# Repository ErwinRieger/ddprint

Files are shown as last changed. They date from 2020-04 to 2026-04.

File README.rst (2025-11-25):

.. raw:: html

   <link rel="stylesheet" href="/images/js_css/asciinema-player.css"" type="text/css"/>

ddPrint - Adding Process control to FDM printers
=================================================

:tags: FDM, 3DDruck, 3dprinting, python, ddprint
:slug: ddprint-3d-printer-firmware

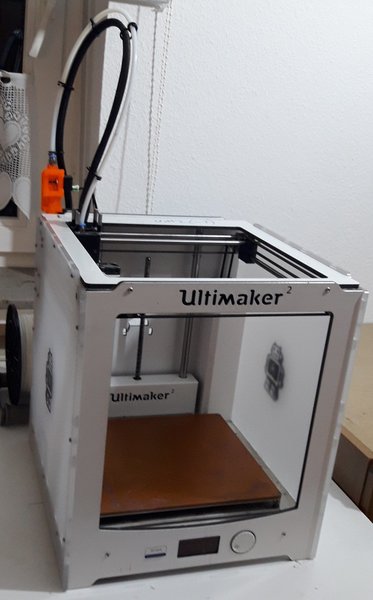
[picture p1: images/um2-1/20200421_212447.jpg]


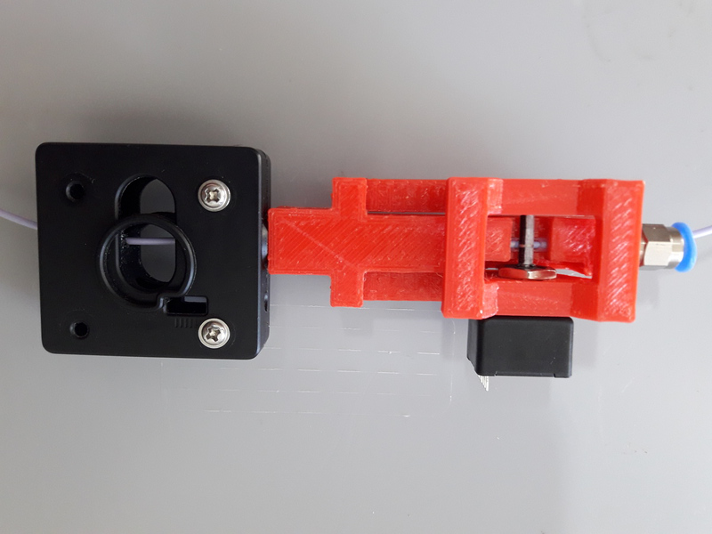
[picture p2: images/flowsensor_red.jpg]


:Note: Work in progress, documentation is incomplete and partly outdated.

Overview
++++++++++

..
   XXX LEVEL 1 XXX

DDPrint adds process control to FDM printer.

The process that is to be controlled is the process of extruding plastic.

The extrusion system includes the feeder, a bowden tube (*) and the hotend with its heater, lets call
this system the *extruder*.

Most FDM printers have no feedback on the extruder part of the printer - they are running *open loop*.

That means to find the balance of printing speed (better: volumetric flow) and hotend temperature
is difficult. Another problem of this *open loop* extrusion system is that the printer cannot react when the
hotend has difficulties to deliver the current demand of flow (for example when printing the first layer or when
the hotend is not hot enough yet).

To close the control loop we add a `sensor <#flowratesensor>`__ to measure the performance of the extruder
und use this data to control the temperature of the hotend and the speed of the printer.

The control loop is closed in two ways, an acvitve way where the speed of the printer is lowered if the hotend cannot 
deliver the demanded flowrate and the feeder begins to slip.
The other is a *feed forward* way: The flowrate sensor is used to measure the characteristics of a given filament - extruder
combination. The result of this measurement is a so called `material profile <#material-profiles>`__.

Control of hotend temperature is called `autotemp <#auto-temp>`__.

Control of printer speed is done with the `temperature-limiter <#temperature-limiter>`__ and the `flowrate-limiter <#flowrate-limiter>`__
.

(*) For the moment `bowden style printers only. <#bowden-style-printers-only>`__

.. contents::

..
   XXX LEVEL 2 XXX

Key features
+++++++++++++

* One of the main features of ddprint: using a flowratesensor 
* Automatic material profile measurement, determine *into-air* and *printing* volumetric flowrate data.
* material profiles
* auto-temp
* temperatuer-limiter.
* flowrate-limiter.
* ddprint uses Integer math instead of floating point because of the weak atmega cpu

Installation
+++++++++++++

Firmware part
-------------

Requirements, dependencies
**************************

* `Arduino-Makefile <https://github.com/sudar/Arduino-Makefile>`__
* avrdude for arduino based firmware upload 
* stm32flash for stm32 based (jennyprinter) firmware upload 

Host part
-------------

The host software is written in Python 3.

Requirements:

* python3
* python3-serial
* python3-numpy
* npyscreen (for the TUI)

Use the `scripts/ddinstall.sh` script to install the dependencies.

Usage
+++++

The host software provides a command line interface (`ddprint`) and a text based user interface (`ddprintui`).

Use the `scripts/dd-fw-upload.sh` script to upload the firmware to the printer.

There are explanatory ansciinema screencasts for the following commands:

* `ddprint getstatus` (shortform: `ddprint stat`)
* `ddprint top`
* `ddprint mon`

Architecture
++++++++++++

The software is split into two main parts:

* The host part where the cpu intensive work (gcode preprocessing, path planning, lookahead, acceleration, advance...) is done.
  The host part is written in Python 3.
* And the firmware part that runs on the ATMega Controller in the printer. This part executes the move commands from
  the host and does other things like the temperature control of the printer.

The firmware part is implemented using the `protothreads-cpp <https://github.com/benhoyt/protothreads-cpp>`__ library.

To overcome the limited memory of the atmega, the unused SD card is converted to something like a *swap device*: It buffers the received data. This decouples the USB transfer
and actual use of the received data, too.

Experimental Features
+++++++++++++++++++++

* RepRap/OctoPrint interface: There is an experimental reprap usbserial interface using a pseudo-tty to use OctoPrint as a frontend for ddPrint. Not much functionality yet: display temperatures and some SD card commands (stubs).
* `reconnect` command: To reconnect to a running printer, works after download is complete, but not if disconnected while downloading stepper data.

Flowratesensor
++++++++++++++

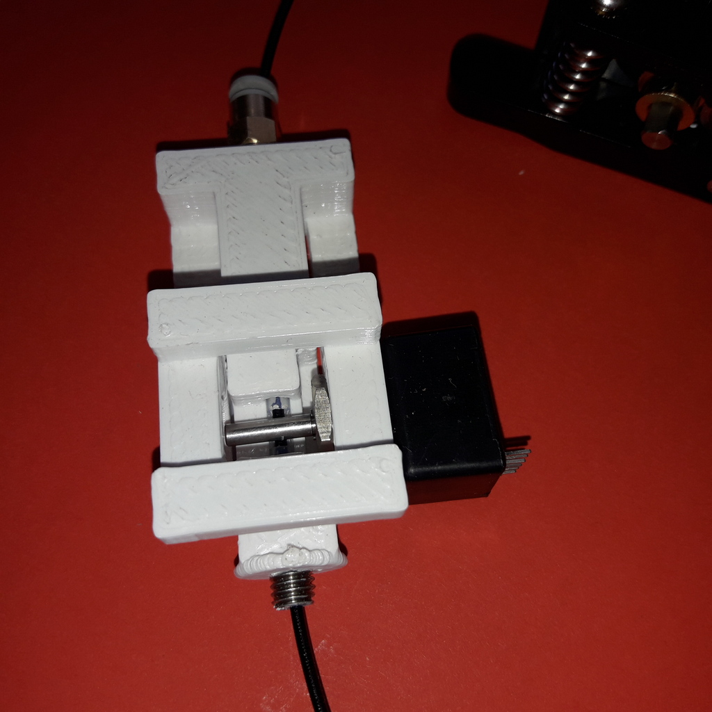
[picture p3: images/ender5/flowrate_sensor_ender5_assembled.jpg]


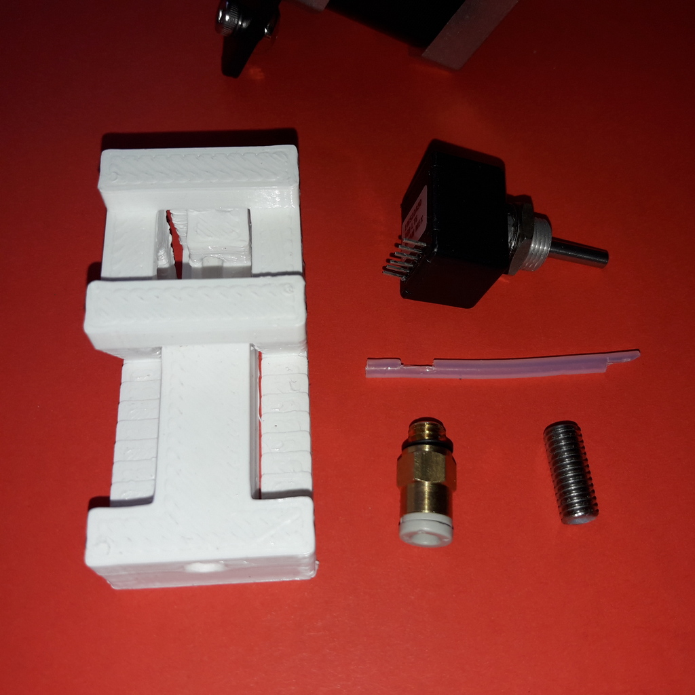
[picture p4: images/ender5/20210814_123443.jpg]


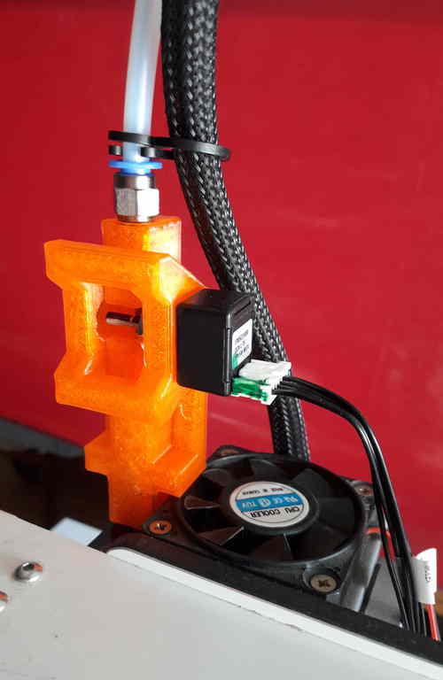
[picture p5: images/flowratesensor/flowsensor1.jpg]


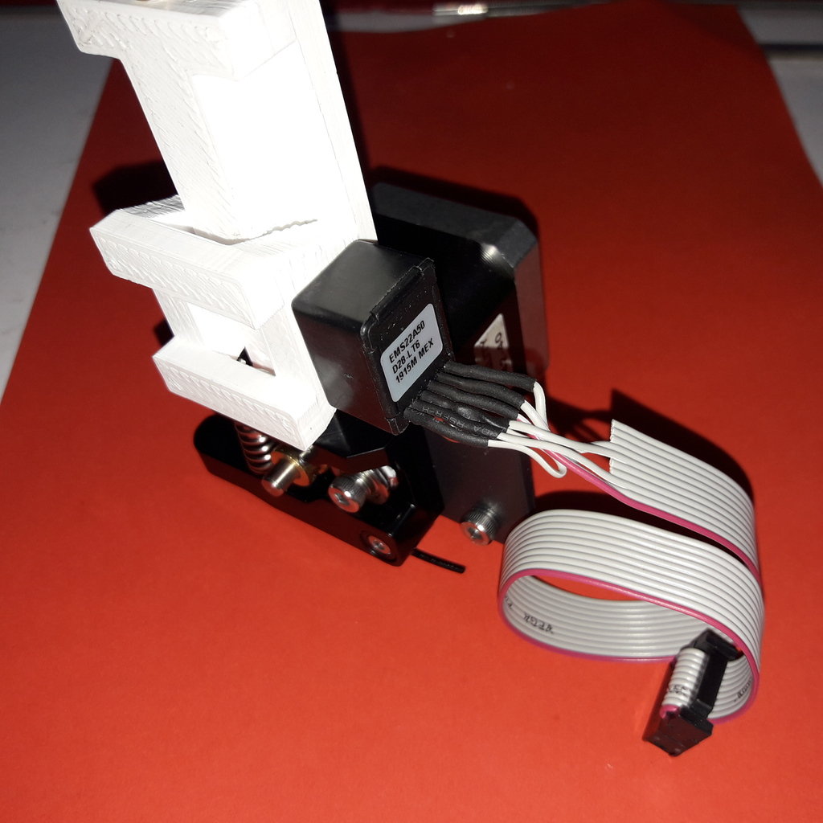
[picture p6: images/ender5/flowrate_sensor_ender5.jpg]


The flowrate sensor (FRS) is used to measure the movement of the filament. It consists of a incremental rotary encoder (Bourns EMS22) and a 3d printed housing.
The axle of the encoder is pressed onto the moving filament using a spring that is part of the FRS housing.

The distance-information from the FRS is continuously read by the firmware and is used for several tasks:

* Compute the speed of the filament and the resulting volumetric flowrate (taking filament diameter into account).
* Compare the actual volumetric flow with the nominal volumetric flow to implement the `flowrate-limiter <#flowrate-limiter>`__.
* Automatically record `material profiles <#material-profiles>`__.
* Automatically `calibrate the feeder "esteps" <#calibrateesteps>`__ (for the machine profile).
* Automatically `calibrate the FRS <#calibratefilsensor>`__ (for the machine profile, too).

More details `are here <#flowratesensor-1>`__.

Bowden style printers only?
+++++++++++++++++++++++++++

For best results, the flowrate sensor has to be placed *after* the feeder. This is easy for a bowden style printer.

For direct driver printers it should be possible but it is more difficult to add the flowrate sensor into the print head (because of
space requirements, heat, added weight and so on).

Material Profiles
+++++++++++++++++

Material (filament) profiles are used for two things in ddprint:

* They define the hotend temperature necessary to melt a given volumetric flow of filament, see `autotemp feature <#auto-temp>`__.
* The `temperature-limiter <#temperature-limiter>`__ uses the information in the material profile to slow down the print in cases
  where the hotend is not hot enough (yet) to melt the requestet amount of filament.

With other words: the material profile gives a picture of the hotend melting capacity for a given machine/filament combination - "*the printer knows its filament*".

A material profile for a given filament is created automatically by ddPrint and stored in JSON format for later use.

This filament-measurement is done in two steps:

* A best-case scenario where filament is extruded *into air*.
* And a worst-case scenario where a small testpart is printed under difficult circumstances (high backpressure because of 100% infill and small layerheight).

ddPrint comes with a python script to plot material profiles (`plot_mat_profile utility <#profile-plotting-utility>`__). Here are two examples of material profiles, one
for a PLA filament and one for a PETg filament:

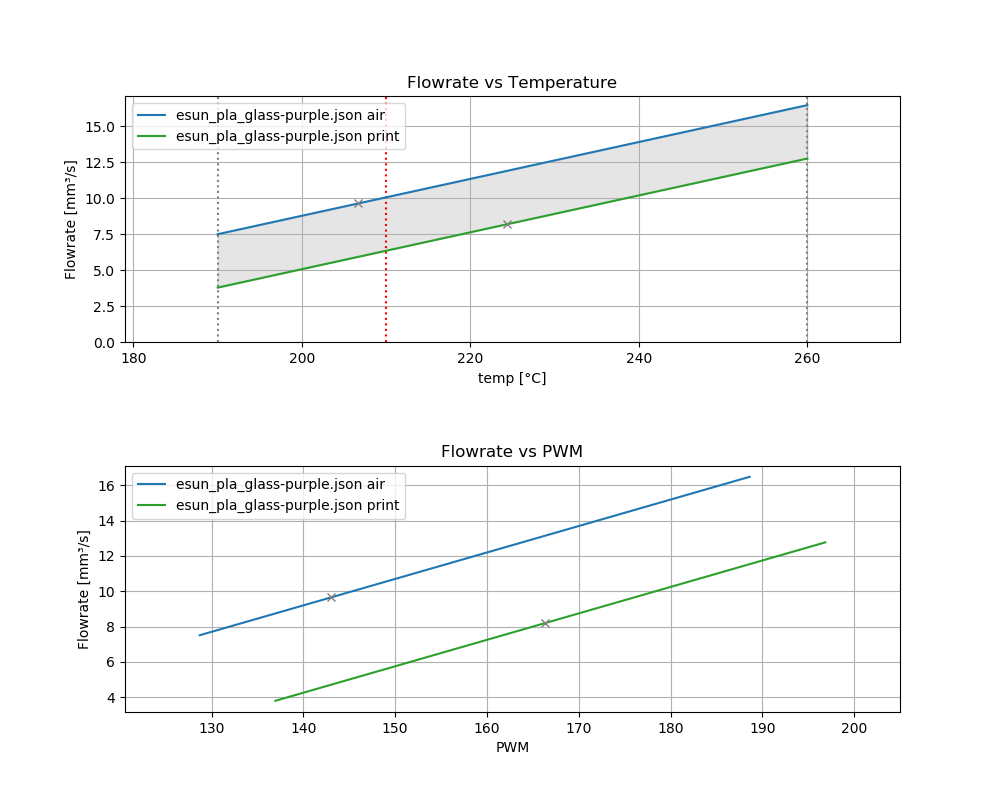
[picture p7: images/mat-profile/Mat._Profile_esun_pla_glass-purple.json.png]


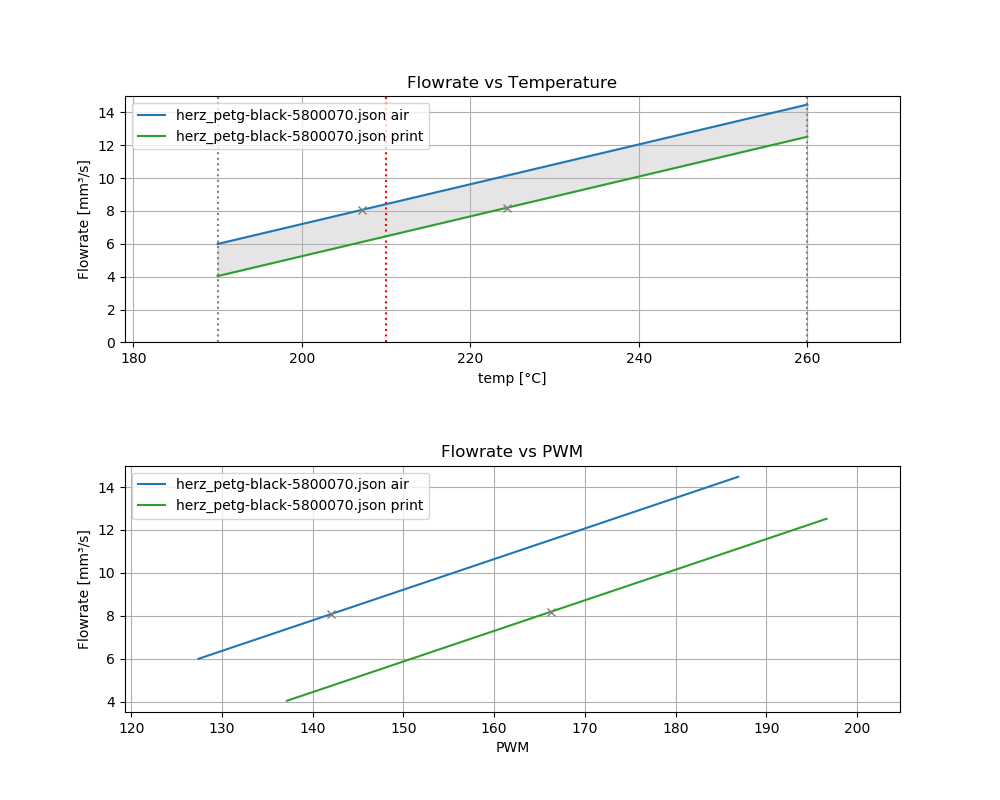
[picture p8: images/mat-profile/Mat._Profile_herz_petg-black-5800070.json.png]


For more details `see here <#material-profiles-1>`__.

Auto Temp
+++++++++++++

While parsing/pathplanning the gcode input, the needed volumetric flowrate is computed. Then the required (minimum) temperature
for this flowrate is determined using a (automatically measured) `material profile <#material-profiles>`__ of the used filament.

So when printing, the temperature of the hotend is dynamically changed in respect to the currently requested flowrate.
This is done in a feed-forward manner because there is a delay between controlling the hotend heater and the change of
temperature in the melting zone/nozzle, of course.

:Note: because of this automatic temperature control, ddPrint ignores bed- and hotend-temperature related commands (M104, M140...) in the gcode input file. When slicing
       your models to be printed with ddPrint you can forget about all the temperature settings there.

The hotend temperature follows the volumentric flow demand given in the input gcode file, is increased for parts of the model where high
flow rates are required and vice-versa.

Temperature limiter
++++++++++++++++++++

The firmware part of ddPrint running on the printer maintains a *temperature-flowrate* table. This table is downloaded from the host to the firmware before
a print is done.

The *temperature-flowrate table* maps hotend temperatures to the max. volumetric flowrates (extruder speed) allowed at a given temperature (for the used
filament). This table is generated from the information found in the material-profile of the used filament (see `material profile <#material-profiles>`__) by the host
part of ddPrint.

If the current hotend temperature is too low for the requested extrusion speed, the speed of the printer (feedrate) is scaled down so that it matches
the achievable flowrate value in the table. This avoids underextrusion (thogether with filament-grinding) and the many problemns related to it.

This is called *temperature limiting*. The temperature-limiter works on a per-printing-move basis, that means this check and a possible slowdown is done
for every straight line of the printhead (essentially for every printing gcode line).

With other words: The *temperature-limiter* together with the `autotemp <#auto-temp>`__ feature ensures that the hotend is always hot enough to
be able to melt the requeste amount of filament.

Flowrate limiter
++++++++++++++++

Similar to the `temperature-limiter <#temperature-limiter>`__ the *flowrate-limiter* slows down the print to avoid underextrusion and grinding of the filament.

It starts to limit the feedrate when the feeder slip is above some threshold, so it uses the *grip value* measured by the `volumetric flowrate sensor <#flowratesensor>`__ (FRS).

Up to 10% of feeder slippage (90% grip) is allowed before the firmware begins to slow down the print. Below 90% grip the feedrate is decreased linearly until reaches
one quater (25%) of the nominal speed, see following plot.

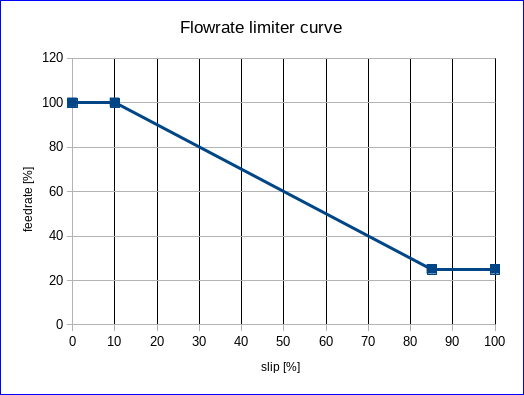
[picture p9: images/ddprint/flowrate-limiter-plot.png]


..
   XXX LEVEL 3 XXX

More in detail
++++++++++++++

Flowratesensor
--------------





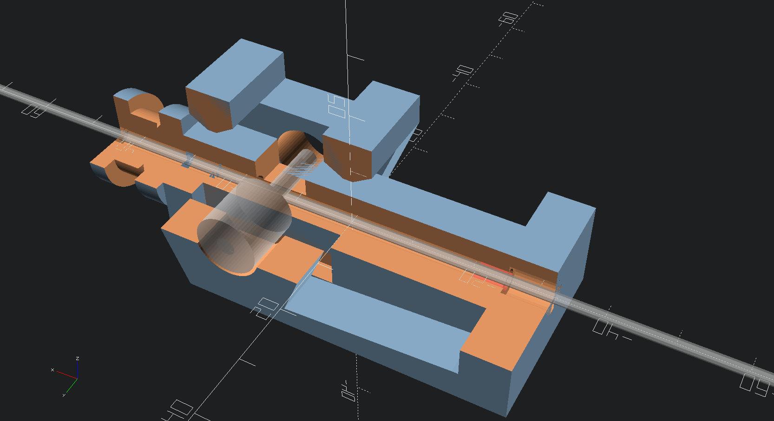
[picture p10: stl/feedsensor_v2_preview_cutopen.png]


The FRS consists of the following components:

* A 3d printed housing (PETg).
* The incremental rotary encoder (EMS22).
* A ptfe inliner with a small cutout to allow the encoder axle to touch the filament.
* A pneumatic coupler to connect the extruder bowden tube to the FRS.
* Depending on the type of the feeder a short piece of a M6 heatbreak to mount the FRS
  at the feeder outlet.
* A cable to connect the FRS to the mainboard of the printer (SPI bus).

The EMS22 rotary encoder has a resolution of 1024 counts per revolution. The diameter of the axle is 3.17mm, this equates
to a overall resolution of about 10µm (0.0097mm) of filament movement per count.

The nominal accuracy of the sensor is 0.7° (about 0.2%), worst case accuracy is 1.4° (about 0.4%). You can find a copy of the EMS22
datasheet (PDF) `here </doc/datasheets/EMS22A.pdf>`__.

The firmware reads the rotary encoder every 10mS, meaning a sample rate of 100Hz.

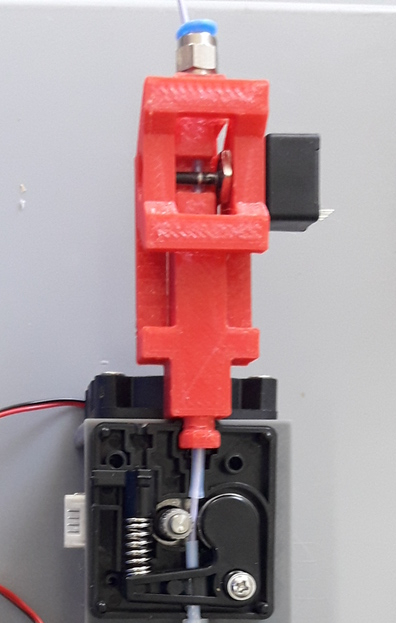
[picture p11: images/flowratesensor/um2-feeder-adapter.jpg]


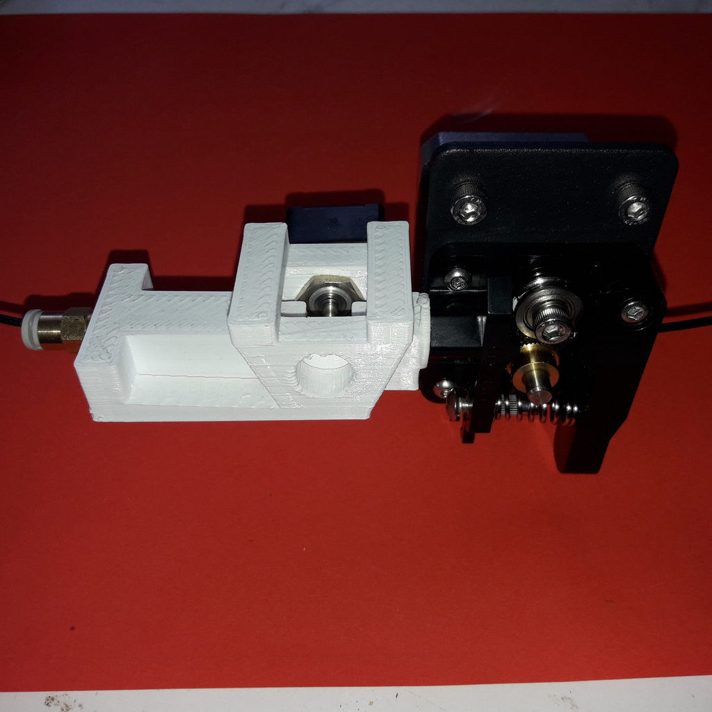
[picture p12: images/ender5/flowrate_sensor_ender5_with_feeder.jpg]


The FRS is mounted at the feeder outlet with an adapter that is part of the FRS housing (BMG or UM2 feeder) or with
a short piece of a M6 heatbreak (Anycubic or Ender feeder) (todo: add bmg style picture).

`Here are some STL files <http://github.com/ErwinRieger/ddprint/tree/master/stl>`__ of the FRS housing.

Material Profiles
-----------------

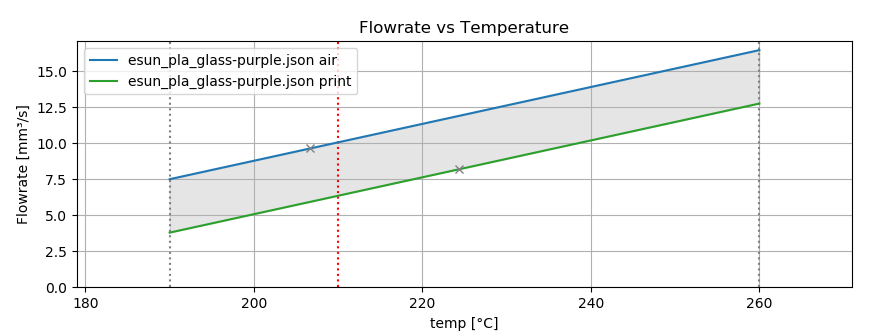
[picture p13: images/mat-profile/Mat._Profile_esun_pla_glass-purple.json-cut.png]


A material profile defines the "melting-capabilites" of a given machine/nozzle/filament combination. It is used by the ddPrint
software to implement the `autotemp <#auto-temp>`__ and the `temperature-limiter <#temperature-limiter>`__ features. The material profile
determines the volumetric flowrate at a given temperature and vice-versa.

Material profiles are generated automatically by ddPrint using the `flowrate sensor <#flowratesensor>`__. This measurement is done
in two steps. This gives us a range of achievable volumetric flowrates for a given filament ("working field", the grey area in the profile plot).

In a first measurement the maximum volumetric flowrate for a given temperature is determined (blue line in material profile plot). This is done by extruding some plastic `into-air <#into-air-filament-measurement>`__, 
without any flow restriction of a printed part. This gives us a best-case flowrate.

The the other end of the flowrate range is measured doing a `real print <#real-print-filament-measurement>`__. In this case the flow through the nozzle is restricted by the part
thats printed. The testpart is sliced using 100% infill and a very low layerheight. This gives us the worst-case flowrate (green line in material profile plot).

:Note: To display a material profile graphically, use the `plot_mat_profile utility <#profile-plotting-utility>`__.

Into-air filament measurement
*****************************



Into-air flowrate (blue line in plot above) is determined using the `measureTempFlowrateCurve <#measure-material-profile-measuretempflowratecurve>`__ command
of the ddPrint program.

To save filament, only two temperature/flowrate points are measured (P1 and P2). One at the lower end of the usable temperature range and one at the top
end (for example, at 200° and 260°). The temperature-flowrate graph is then aproximated using this two points, they define a straight line equation y = M*x + C1.

The steps to measure *into-air flowrate data* are are:

* User loads the filament to test and starts measurement.
* ddPrint heats the hotend to the lower temperature.
* When start-temperature is reached, the PWM value of the hotend heater is fixed (PID temp control is disabled) and
  ddPrint starts to extrude filament at a low flowrate.
* Then in a loop, the flowrate is increased while watching the feeder grip.
* While increasing the flowrate, the feeder grip will decrease because of the rising
  backpressure from the filament pressed through the nozzle.
* At some point, feeder grip drops below a pre-defined value called *minGrip*, 90% for example.
* Flowrate is no longer increased, the first measurement point P1 is determined.
* PID temperature control is re-enabled and hotend is heated to the upper temp.
* When this upper temperature is reached, the measurement loop starts again. PWM is fixed and
  flowrate is increased while watching feeder grip.
* When feeder grip falls below *minGrip* the second time, we have determined the second
  measurement point P2.
* Hotend is switched off and the speed of the extruder is gracefully decreased until stop.
* The final step is to compute the values of M and C1 and write the *into-air flowrate data* to a material profile template file.

Real print filament measurement
********************************



This is similar to the *into-air* measurement, but this time doing a real print. The result is the *worst case flowrate data* (the green line in the plot above).

The ddPrint command for this measurement is `measureTempFlowrateCurve2 <#measure-material-profile-measuretempflowratecurve2>`__.

Again a straight line equation y = M*x + C2 is determined. To save filament, only one temperature/flowrate point is measured (P3). As a simplification,
we assume the same slope as in the *into-air* measurement.

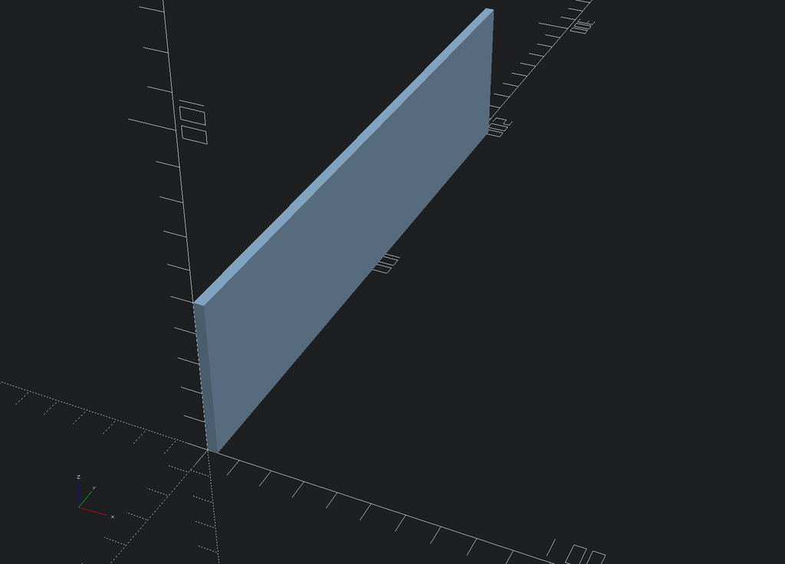
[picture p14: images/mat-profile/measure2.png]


The test-part printed is designed and sliced as follows:

* The part is tall to quickly gain height, this is to minimize the heating influence of the heated bed.
* It is long in one direction to help the flowrate measurement (long straight lines with constant extrusion, minimize acceleration effects).
* It is sliced with 100% infill for high nozzle backpressure.
* It is sliced with a small layer-height for high nozzle backpressure.
* It is sliced with a high feedrate, again for high nozzle backpressure.

:Note: The test-part is not printed to its full height, measurement will stop before.

The steps to measure *printing flowrate data* are are:

* Filament to test is loaded, printer is prepared to do a print and user starts measurement.
* ddPrint heats the hotend to a temperature in the middle of the usable temperature range.
* When start-temperature is reached, the PWM value of the hotend heater is fixed (PID temp control is disabled) and
  ddPrint starts to print the testpart using a low speed/flowrate.
* Print until some height is reached to minimize heating bed effects.
* Then in a loop, the flowrate is increased on every layer while watching the feeder grip.
* While increasing the flowrate, the feeder grip will decrease because of the rising
  backpressure from the filament pressed through the nozzle (additionally restricted by the part thats printed).
* At some point, feeder grip drops below a pre-defined value called *minGrip*, 90% for example.
* Measurement ends, datapoint P3 is determined.
* Print is gracefully stopped.
* The final step is to write the *printing flowrate data* (together with the *into-air data*) to a material profile template file.

After editing the newly measured material-profile (.json file) it can be renamed and stored somewhere in a profiles folder for
later view (`plot_mat_profile utility <#profile-plotting-utility>`__) or use (printing).

Workingpoint (strength) parameter
**********************************

The `autotemp <#auto-temp>`__ feature splits the print into segements and determines the necessary temperature for theese
segments using the given material profile. It then adds the corresponding temperature control commands into the datastream
sent to the printer. This is done in a feed-forward fashion, the temperature is set some time before the segment is
printed.

When looking up the needed temperature in the material profile, the following question arises: Which
temperature should be used, the one belonging to the into-air measurement, the one from the real-print measurement or
a temperature somewhere in between?

The next picture illustrates this. In this example, we want to know the necessary temperature for a volumetric
flowrate of 9 mm³/s (pink horizontal line).

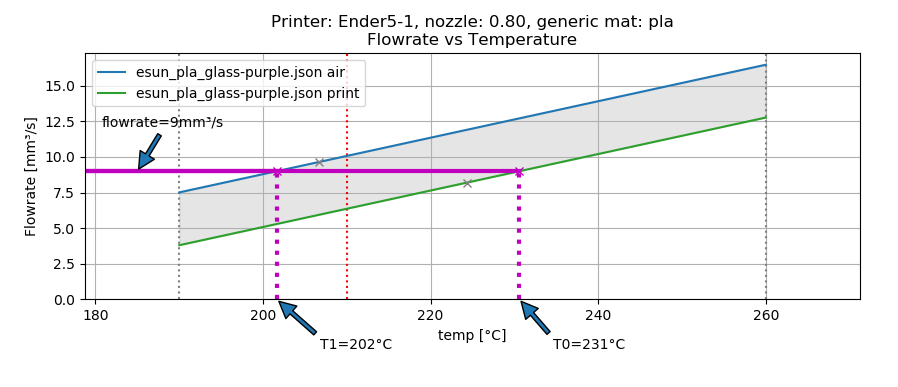
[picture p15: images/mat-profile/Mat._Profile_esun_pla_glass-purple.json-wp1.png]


As we can see, the into-air temperature for this flowrate would be 202 °C (T1) and the real-print temp is 231 °C (T0).

This is where the *workingpoint* parameter comes into play. The workingpoint (WP) parameter tells ddPrint which temperature
to choose. WP is a value in the range 0...1 an can be specified as a commandline parameter or through a experimental
G-Code command (M901). When WP is 0 then the temperature belonging to the real-print graph is used and when WP is 1 then
the into-air temperature is used. Other values of WP use the according temperature between T0 and T1.

The default value of WP is 0.5, the corresponding graph looks like this:

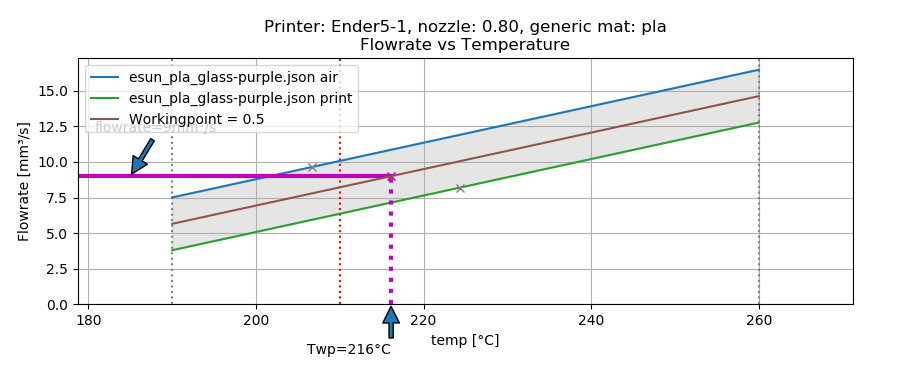
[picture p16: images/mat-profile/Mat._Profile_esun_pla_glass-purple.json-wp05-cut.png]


With WP=0.5, the autotemp feature of ddPrint uses temperatures in the middle of the two graphs, the corresponding function
is shown as the brown linegraph. Hotend temperature for flowrate 9 mm³/s in this case is 216 °C.

With other words, with the workingpoint parameter we can:

* Control the temperature level the autotemp feature is using througout the print.
* Control the quality of the print, *look VS strength tradeof*.

WP values towards zero are increasing the temperature level, resulting in better layerbonding and stronger
parts (good for functional parts). WP values towards one are lowering the resulting temperatures, resulting in
a better look of the printed parts (better for figurines and the like).

Two examples with a volumetric flowrate of 9 mm³/s and working points 0.3 (hotter than default WP 0.5) and
0.8 (cooler than default WP 0.5):

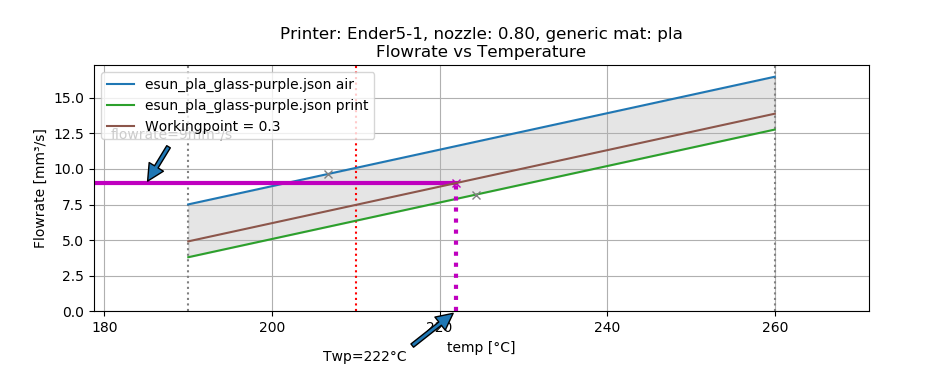
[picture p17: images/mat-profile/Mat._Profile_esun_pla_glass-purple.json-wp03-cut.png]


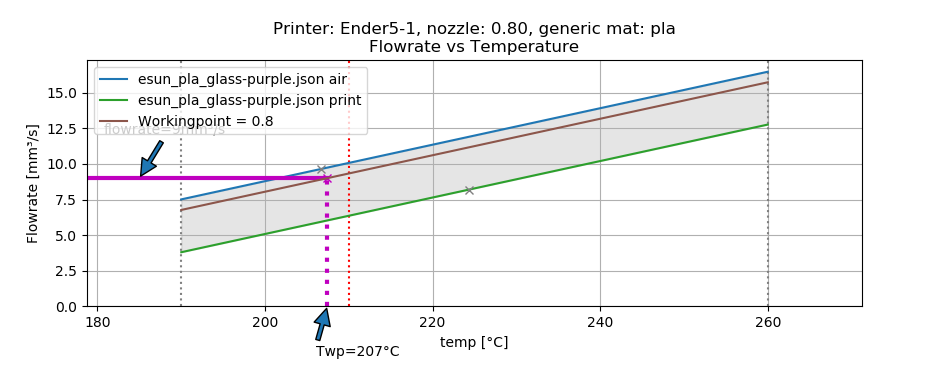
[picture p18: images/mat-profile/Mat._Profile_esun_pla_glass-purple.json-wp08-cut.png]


When workingpoint value is set to zero, then the real-print measurement graph is used (brown linegraph laying on the
green graph). Accordingly when WP is one, the into-air measurement grap is used (brown linegraph laying on the blue graph).

TBD: note about PWM values/graph, link to think in terms of energy.

Think in terms of energy
********************************

TBD: think more in terms of energy (hotend PWM) instead of temperature.

Profile plotting utility
********************************

TBD: describe *plot_mat_profile* utility.

.. code-block:: sh

      usage: plot_mat_profile.py [-h] printer nozzle mat smat [smat ...]

      plot_mat_profile.py - plot ddPrint material profiles.

      positional arguments:
        printer     Name of printer to select profiles.
        nozzle      Name of nozzle profile to use [nozzle40, nozzle80...].
        mat         Name of generic material profile to use [pla, petg...].
        smat        Material profile(s) to plot.

      optional arguments:
        -h, --help  show this help message and exit

---------------------------------------------------------------------------------------------

.. raw:: html

    <script type='text/javascript' src='/images/Widget_2.js'></script>
    <script type='text/javascript' src='/images/kofiButton.js'></script>
    <script src="/images/js_css/asciinema-player.js"></script>

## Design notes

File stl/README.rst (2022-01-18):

Volumetric flowrate sensor STL models
=====================================

Here are some 3D models for the ddPrint flowrate sensor.

Base FRS model is always the same. It is combined with different inlet- and outlet-adapters.

The inlet is where the FRS is mouted at the feeder, possible feeders are:

* UM2: the old (black) Ultimaker 2 feeder.
* E3D: E3D adapter (for example on the Titan feeder), used on BMG style feeders too.
* M6: FRS is connected to the feeder using a short piece of a M6 heatbreak, for example
  Ender or Anycubic i3m.

The outlet side of the FRS is where the filament bowden tube is connected. It is a hole where
a M6 or M10 pneumatic coupler (pushfit) is screwd in.

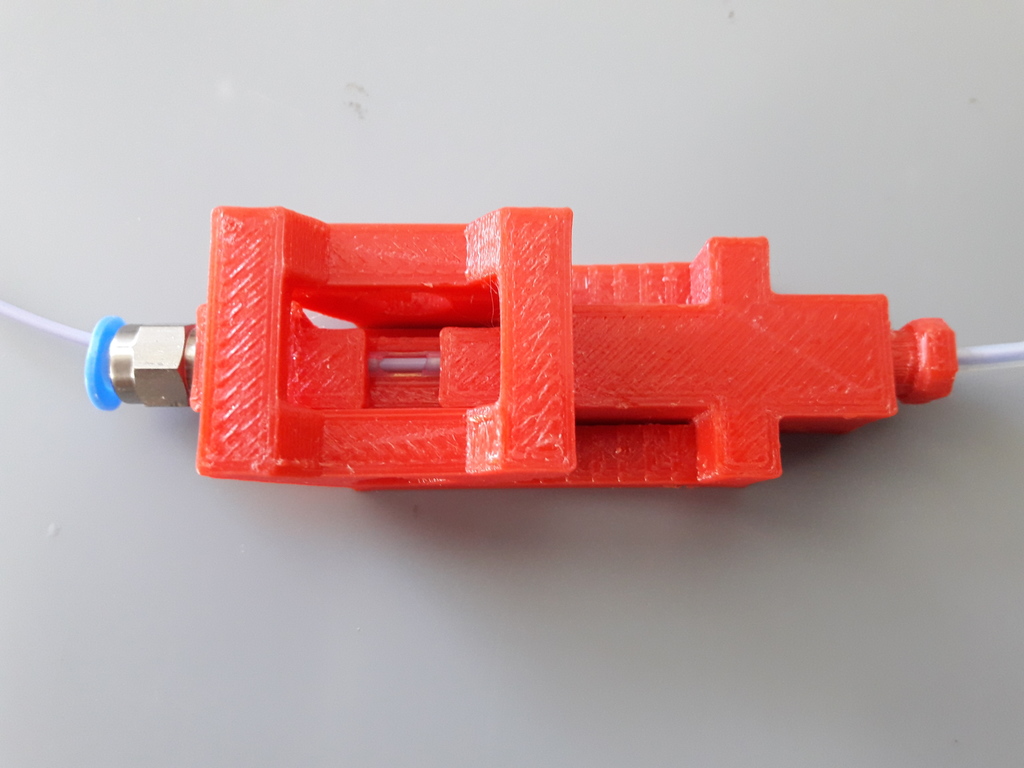
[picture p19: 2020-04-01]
images/flowratesensor/with_filament.jpg

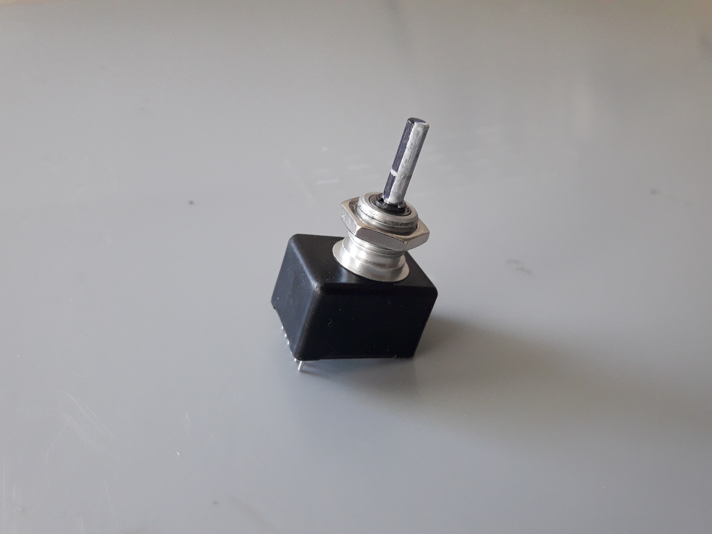
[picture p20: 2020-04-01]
images/flowratesensor/bourns_incremental_sensor.jpg

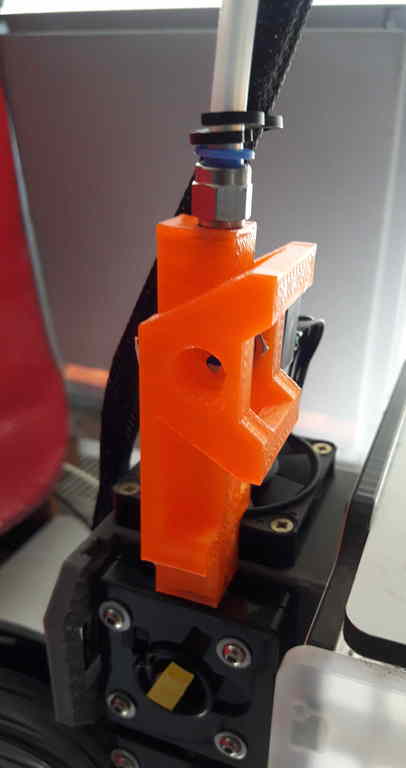
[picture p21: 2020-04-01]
images/flowratesensor/flowsensor2.jpg

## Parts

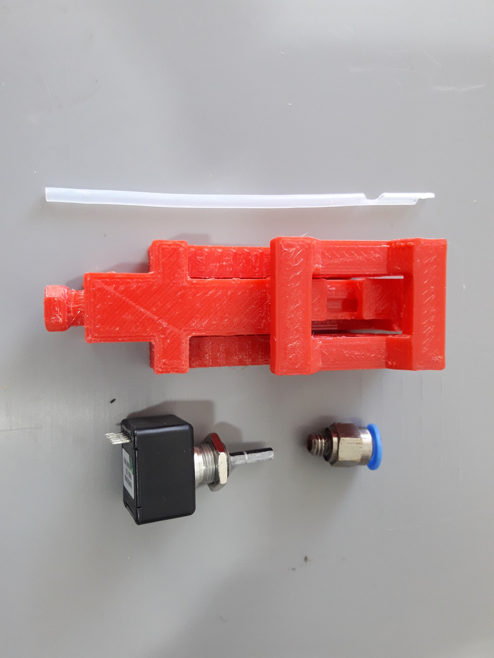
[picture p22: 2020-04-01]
images/flowratesensor/flowratesensor_parts.jpg

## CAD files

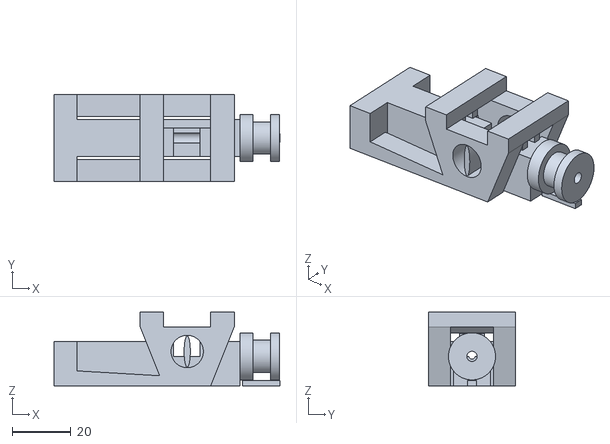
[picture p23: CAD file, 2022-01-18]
stl/feedsensor-in_E3D-out_M6.stl
76.8 x 29.7 x 25.0

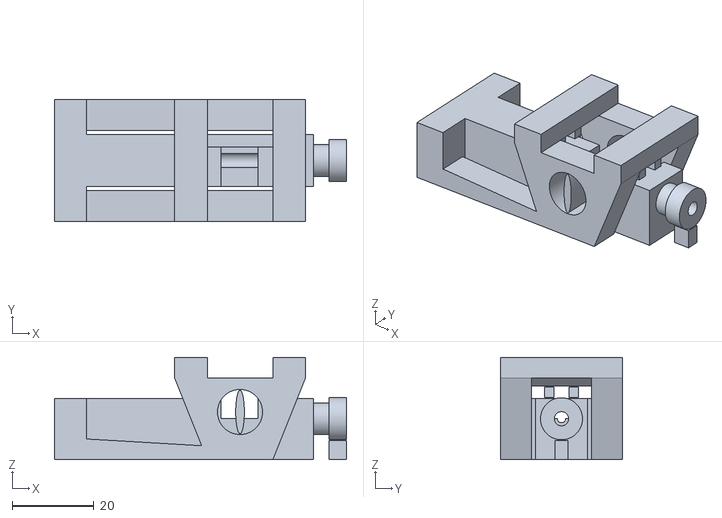
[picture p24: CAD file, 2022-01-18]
stl/feedsensor-in_UM2-out_M6.stl
71.3 x 29.7 x 25.0

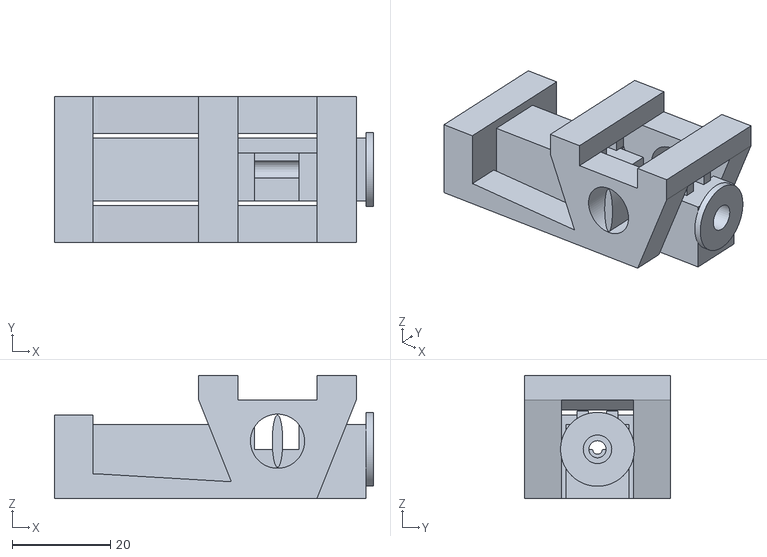
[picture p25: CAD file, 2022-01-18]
stl/feedsensor-in_M6-out_M10.stl
64.8 x 29.7 x 25.0

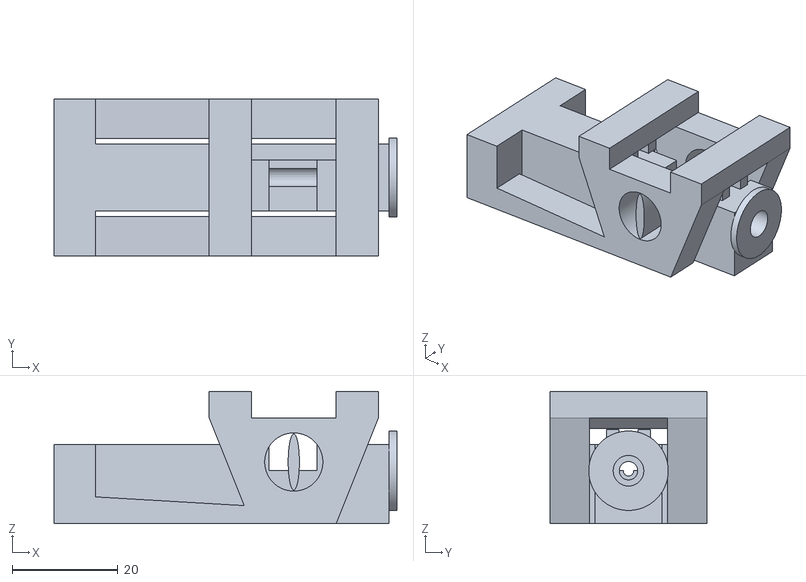
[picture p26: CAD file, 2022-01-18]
stl/feedsensor-in_M6-out_M6.stl
64.8 x 29.7 x 25.0

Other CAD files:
stl/feedsensor-in_UM2-out_M10.stl
stl/feedsensor-in_E3D-out_M10.stl

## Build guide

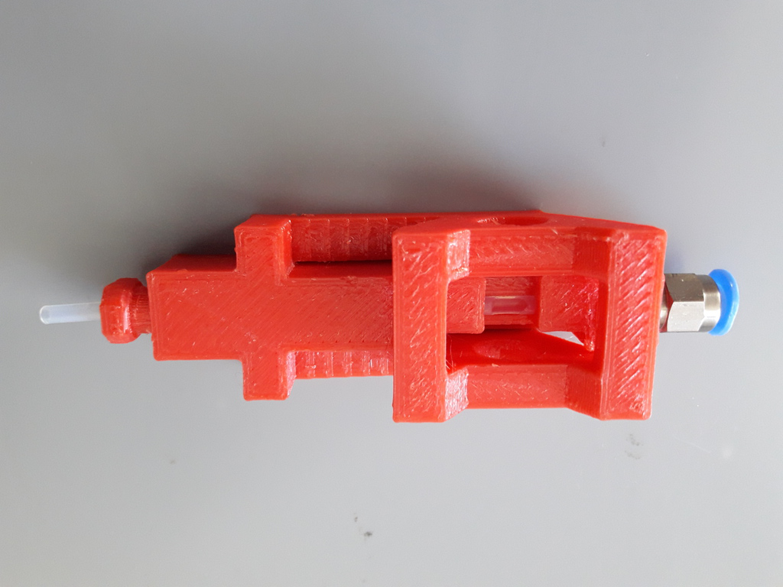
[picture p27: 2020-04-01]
images/flowratesensor/teflonliner_pneumaticconn_installed.jpg

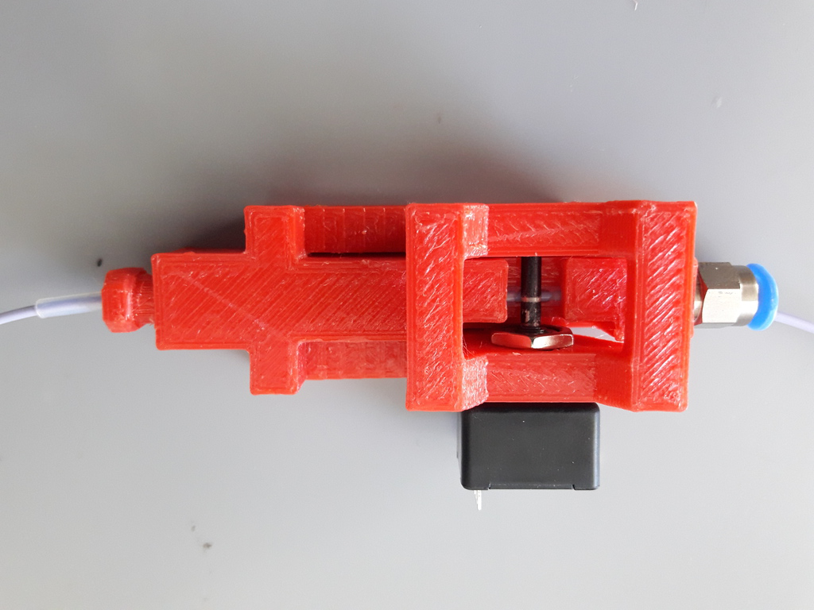
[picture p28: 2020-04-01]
images/flowratesensor/sensor_installed.jpg

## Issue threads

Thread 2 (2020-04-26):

Improve hotend PID

ErwinRieger, 2020-04-26:
Look into http://brettbeauregard.com/blog/2011/04/improving-the-beginners-pid-introduction/ and see if pid algorithm can be improved.
Maybe http://brettbeauregard.com/blog/2011/04/improving-the-beginners-pid-introduction/, http://brettbeauregard.com/blog/2017/06/proportional-on-measurement-the-code/ can be used to avoid temperature overshots. Maybe faster material profile measurement possible.

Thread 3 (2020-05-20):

Sometimes hotend is not switched off after print finished

ErwinRieger, 2020-05-20:
Seems to be related to hotend feed forward pulsing.

ErwinRieger, 2020-07-08:
Bug no longer exists because the respective code was replaced with the feed forward temp control.

Closed 2020-07-08.

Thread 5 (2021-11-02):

No locking on serial port.

ErwinRieger, 2021-11-02:
There is no locking mechanism on the serial port (ttyUSBx/ttyACMx), yet. Starting a second instance of ddprint will disturb the connection of the first instance. This results in a failed print (if not all gcode is processed and downloaded to the printer).

ErwinRieger, 2022-02-10:
Fixed with fad9c34ebd64f67783a75b753c2a31bcb07bd328 (in next branch), use exlusive mode of pyserial.
Will close this issue when merged into master.

ErwinRieger, 2022-04-03:
Fix merged to master, closing.

Closed 2022-04-03.

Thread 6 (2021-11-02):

Endofprint: turn of heaters with a synchronized command

ErwinRieger, 2021-11-02:
Currently the host process is responsible to switch off heaters after print finishes. This leads to running heaters if the host process dies, even if the print finishes successfully.
Use a synchronized command and let the printer turn off it's heaters after print.

ErwinRieger, 2022-02-09:
Fixed with b6397fe95195733edffeef0d32d2b02afb727577 (in next branch), use syncronized command to switch of heaters at end of print.
Will close this issue when merged into master.

ErwinRieger, 2022-04-03:
Fix merged to master, closing.

Closed 2022-04-03.

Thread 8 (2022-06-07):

Jennyprinter: sporadic error, print stops halfways

ErwinRieger, 2022-06-07:
Jennyprinter: sporadic error, print stops halfways

Firmware seems to run normally, just the processing of the stepbuffer stops. Maybe irq-related.

ErwinRieger, 2022-07-01:
There was an error in the computation of RawStepData (sign-error).

Fixed in 84e985e82c729ff7f2f84c2d3c1748afc1825777 (in next branch).

Will close this issue when merged into master.

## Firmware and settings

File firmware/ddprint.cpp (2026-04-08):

/*
 * This file is part of ddprint - a direct drive 3D printer firmware.
 * 
 * Copyright 2015 erwin.rieger@ibrieger.de
 * 
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
 * You should have received a copy of the GNU General Public License
 * along with ddprint.  If not, see <http://www.gnu.org/licenses/>.
 */

/*
 * Todo jennyprinter port:
 * * swapdevice: add sanity test sectorsize != 512 bytes?
 * * usb: some flash sticks seem to hang at getReady cmd (add timeout / testUnitReadyRetry)
 * * cleanup task info stuff
 */

#include <Arduino.h>

#include <limits.h>

#include "crc16.h"

#include "ddprint.h"
#include "rxbuffer.h"
#include "txbuffer.h"
#include "temperature.h"
#include "ddtemp.h"
#include "swapdev.h"
#include "filsensor.h"
#include "ddcommands.h"
#include "ddlcd.h"
#include "stepper.h"

#include "protothreads-cpp/Protothread.h"

//The ASCII buffer for recieving from SD:
#define SD_BUFFER_SIZE 512

// Macro to read scalar types from a buffer
#define FromBuf(typ, adr) ( * ((typ *)(adr)))

#define X_SW_ENDSTOP_PRESSED ((current_pos_steps[X_AXIS] < 0) || (current_pos_steps[X_AXIS] > (int32_t)printer.getHostSettings().buildVolX))
#define Y_SW_ENDSTOP_PRESSED ((current_pos_steps[Y_AXIS] < 0) || (current_pos_steps[Y_AXIS] > (int32_t)printer.getHostSettings().buildVolY))
#define Z_SW_ENDSTOP_PRESSED ((current_pos_steps[Z_AXIS] < 0) || (current_pos_steps[Z_AXIS] > (int32_t)printer.getHostSettings().buildVolZ))

// Debug
#if  defined(DEBUGPROCSTAT)

enum LoopTasks { TaskIdle, TaskTempControl, TaskHeater, TaskFilSensor, TaskUsbInput, TaskUsbOutput, TaskSwapDev, TaskFillBuffer, TaskSum};

static struct TaskTiming taskTiming[9] = { 
    { 0, 0, 0, 0 },         // Idle time between loop() calles
    { 0, 0, 0, 0 },         // Temperature measurement
    { 0, 0, 0, 0 },         // Heater temperature control
    { 0, 0, 0, 0 },         // Filament sensor readings (flowrate measurement)
    { 0, 0, 0, 0 },         // USB input
    { 0, 0, 0, 0 },         // USB output
    { 0, 0, 0, 0 },         // Mass storage IO 
    { 0, 0, 0, 0 },         // Read *swapdev* and fill *stepbuffer*
    { 0, 0, 0, 0 },         // Summary of all these tasks
};
#endif


/////////////////////////////////////////////////////////////////////////////////////
// #if defined(USEExtrusionRateTable)

static int16_t extrusionLimitBaseTemp = 170;

//
// Limit extrusion rate by the hotend temperature.
//
// Generated by snippets/genTempTable.py
static uint16_t tempExtrusionRateTable[NExtrusionLimit];

#if 0

= {
    /* Temp: 170.000000, max flowrate: 0.1 mm³/s, max espeed: 0.0 mm/s, steps/s: 5, steprate: 170587 us, timervalue: */ 65535,
    /* Temp: 171.000000, max flowrate: 0.5 mm³/s, max espeed: 0.2 mm/s, steps/s: 29, steprate: 34117 us, timervalue: */ 65535,
    /* Temp: 172.000000, max flowrate: 0.9 mm³/s, max espeed: 0.4 mm/s, steps/s: 52, steprate: 18954 us, timervalue: */ 37908,
    /* Temp: 173.000000, max flowrate: 1.3 mm³/s, max espeed: 0.5 mm/s, steps/s: 76, steprate: 13122 us, timervalue: */ 26244,
    /* Temp: 174.000000, max flowrate: 1.7 mm³/s, max espeed: 0.7 mm/s, steps/s: 99, steprate: 10034 us, timervalue: */ 20069,
    /* Temp: 175.000000, max flowrate: 2.1 mm³/s, max espeed: 0.9 mm/s, steps/s: 123, steprate: 8123 us, timervalue: */ 16246,
    /* Temp: 176.000000, max flowrate: 2.5 mm³/s, max espeed: 1.0 mm/s, steps/s: 146, steprate: 6823 us, timervalue: */ 13646,
    /* Temp: 177.000000, max flowrate: 2.9 mm³/s, max espeed: 1.2 mm/s, steps/s: 170, steprate: 5882 us, timervalue: */ 11764,
    /* Temp: 178.000000, max flowrate: 3.3 mm³/s, max espeed: 1.4 mm/s, steps/s: 193, steprate: 5169 us, timervalue: */ 10338,
    /* Temp: 179.000000, max flowrate: 3.7 mm³/s, max espeed: 1.5 mm/s, steps/s: 216, steprate: 4610 us, timervalue: */ 9220,
    /* Temp: 180.000000, max flowrate: 4.1 mm³/s, max espeed: 1.7 mm/s, steps/s: 240, steprate: 4160 us, timervalue: */ 8321,
    /* Temp: 181.000000, max flowrate: 4.5 mm³/s, max espeed: 1.9 mm/s, steps/s: 263, steprate: 3790 us, timervalue: */ 7581,
    /* Temp: 182.000000, max flowrate: 4.9 mm³/s, max espeed: 2.0 mm/s, steps/s: 287, steprate: 3481 us, timervalue: */ 6962,
    /* Temp: 183.000000, max flowrate: 5.3 mm³/s, max espeed: 2.2 mm/s, steps/s: 310, steprate: 3218 us, timervalue: */ 6437,
    /* Temp: 184.000000, max flowrate: 5.7 mm³/s, max espeed: 2.4 mm/s, steps/s: 334, steprate: 2992 us, timervalue: */ 5985,
    /* Temp: 185.000000, max flowrate: 6.1 mm³/s, max espeed: 2.5 mm/s, steps/s: 357, steprate: 2796 us, timervalue: */ 5593,
    /* Temp: 186.000000, max flowrate: 6.5 mm³/s, max espeed: 2.7 mm/s, steps/s: 381, steprate: 2624 us, timervalue: */ 5248,
    /* Temp: 187.000000, max flowrate: 6.9 mm³/s, max espeed: 2.9 mm/s, steps/s: 404, steprate: 2472 us, timervalue: */ 4944,
    /* Temp: 188.000000, max flowrate: 7.3 mm³/s, max espeed: 3.0 mm/s, steps/s: 427, steprate: 2336 us, timervalue: */ 4673,
    /* Temp: 189.000000, max flowrate: 7.7 mm³/s, max espeed: 3.2 mm/s, steps/s: 451, steprate: 2215 us, timervalue: */ 4430,
    /* Temp: 190.000000, max flowrate: 8.1 mm³/s, max espeed: 3.4 mm/s, steps/s: 474, steprate: 2106 us, timervalue: */ 4212,
    /* Temp: 191.000000, max flowrate: 8.5 mm³/s, max espeed: 3.5 mm/s, steps/s: 498, steprate: 2006 us, timervalue: */ 4013,
    /* Temp: 192.000000, max flowrate: 8.9 mm³/s, max espeed: 3.7 mm/s, steps/s: 521, steprate: 1916 us, timervalue: */ 3833,
    /* Temp: 193.000000, max flowrate: 9.3 mm³/s, max espeed: 3.9 mm/s, steps/s: 545, steprate: 1834 us, timervalue: */ 3668,
    /* Temp: 194.000000, max flowrate: 9.7 mm³/s, max espeed: 4.0 mm/s, steps/s: 568, steprate: 1758 us, timervalue: */ 3517,
    /* Temp: 195.000000, max flowrate: 10.1 mm³/s, max espeed: 4.2 mm/s, steps/s: 592, steprate: 1688 us, timervalue: */ 3377,
    /* Temp: 196.000000, max flowrate: 10.5 mm³/s, max espeed: 4.4 mm/s, steps/s: 615, steprate: 1624 us, timervalue: */ 3249,
    /* Temp: 197.000000, max flowrate: 10.9 mm³/s, max espeed: 4.5 mm/s, steps/s: 638, steprate: 1565 us, timervalue: */ 3130,
    /* Temp: 198.000000, max flowrate: 11.3 mm³/s, max espeed: 4.7 mm/s, steps/s: 662, steprate: 1509 us, timervalue: */ 3019,
    /* Temp: 199.000000, max flowrate: 11.7 mm³/s, max espeed: 4.9 mm/s, steps/s: 685, steprate: 1458 us, timervalue: */ 2916,
    /* Temp: 200.000000, max flowrate: 12.1 mm³/s, max espeed: 5.0 mm/s, steps/s: 709, steprate: 1409 us, timervalue: */ 2819,
    /* Temp: 201.000000, max flowrate: 12.5 mm³/s, max espeed: 5.2 mm/s, steps/s: 732, steprate: 1364 us, timervalue: */ 2729,
    /* Temp: 202.000000, max flowrate: 12.9 mm³/s, max espeed: 5.4 mm/s, steps/s: 756, steprate: 1322 us, timervalue: */ 2644,
    /* Temp: 203.000000, max flowrate: 13.3 mm³/s, max espeed: 5.5 mm/s, steps/s: 779, steprate: 1282 us, timervalue: */ 2565,
    /* Temp: 204.000000, max flowrate: 13.7 mm³/s, max espeed: 5.7 mm/s, steps/s: 803, steprate: 1245 us, timervalue: */ 2490,
    /* Temp: 205.000000, max flowrate: 14.1 mm³/s, max espeed: 5.9 mm/s, steps/s: 826, steprate: 1209 us, timervalue: */ 2419,
    /* Temp: 206.000000, max flowrate: 14.5 mm³/s, max espeed: 6.0 mm/s, steps/s: 850, steprate: 1176 us, timervalue: */ 2352,
    /* Temp: 207.000000, max flowrate: 14.9 mm³/s, max espeed: 6.2 mm/s, steps/s: 873, steprate: 1144 us, timervalue: */ 2289,
    /* Temp: 208.000000, max flowrate: 15.3 mm³/s, max espeed: 6.4 mm/s, steps/s: 896, steprate: 1114 us, timervalue: */ 2229,
    /* Temp: 209.000000, max flowrate: 15.7 mm³/s, max espeed: 6.5 mm/s, steps/s: 920, steprate: 1086 us, timervalue: */ 2173,
    /* Temp: 210.000000, max flowrate: 16.1 mm³/s, max espeed: 6.7 mm/s, steps/s: 943, steprate: 1059 us, timervalue: */ 2119,
    /* Temp: 211.000000, max flowrate: 16.5 mm³/s, max espeed: 6.9 mm/s, steps/s: 967, steprate: 1033 us, timervalue: */ 2067,
    /* Temp: 212.000000, max flowrate: 16.9 mm³/s, max espeed: 7.0 mm/s, steps/s: 990, steprate: 1009 us, timervalue: */ 2018,
    /* Temp: 213.000000, max flowrate: 17.3 mm³/s, max espeed: 7.2 mm/s, steps/s: 1014, steprate: 986 us, timervalue: */ 1972,
    /* Temp: 214.000000, max flowrate: 17.7 mm³/s, max espeed: 7.4 mm/s, steps/s: 1037, steprate: 963 us, timervalue: */ 1927,
    /* Temp: 215.000000, max flowrate: 18.1 mm³/s, max espeed: 7.5 mm/s, steps/s: 1061, steprate: 942 us, timervalue: */ 1884,
    /* Temp: 216.000000, max flowrate: 18.5 mm³/s, max espeed: 7.7 mm/s, steps/s: 1084, steprate: 922 us, timervalue: */ 1844,
    /* Temp: 217.000000, max flowrate: 18.9 mm³/s, max espeed: 7.9 mm/s, steps/s: 1107, steprate: 902 us, timervalue: */ 1805,
    /* Temp: 218.000000, max flowrate: 19.3 mm³/s, max espeed: 8.0 mm/s, steps/s: 1131, steprate: 883 us, timervalue: */ 1767,
    /* Temp: 219.000000, max flowrate: 19.7 mm³/s, max espeed: 8.2 mm/s, steps/s: 1154, steprate: 865 us, timervalue: */ 1731,
    /* Temp: 220.000000, max flowrate: 20.1 mm³/s, max espeed: 8.4 mm/s, steps/s: 1178, steprate: 848 us, timervalue: */ 1697,
    /* Temp: 221.000000, max flowrate: 20.5 mm³/s, max espeed: 8.5 mm/s, steps/s: 1201, steprate: 832 us, timervalue: */ 1664,
    /* Temp: 222.000000, max flowrate: 20.9 mm³/s, max espeed: 8.7 mm/s, steps/s: 1225, steprate: 816 us, timervalue: */ 1632,
    /* Temp: 223.000000, max flowrate: 21.3 mm³/s, max espeed: 8.9 mm/s, steps/s: 1248, steprate: 800 us, timervalue: */ 1601,
    /* Temp: 224.000000, max flowrate: 21.7 mm³/s, max espeed: 9.0 mm/s, steps/s: 1272, steprate: 786 us, timervalue: */ 1572,
    /* Temp: 225.000000, max flowrate: 22.1 mm³/s, max espeed: 9.2 mm/s, steps/s: 1295, steprate: 771 us, timervalue: */ 1543,
    /* Temp: 226.000000, max flowrate: 22.5 mm³/s, max espeed: 9.4 mm/s, steps/s: 1318, steprate: 758 us, timervalue: */ 1516,
    /* Temp: 227.000000, max flowrate: 22.9 mm³/s, max espeed: 9.5 mm/s, steps/s: 1342, steprate: 744 us, timervalue: */ 1489,
    /* Temp: 228.000000, max flowrate: 23.3 mm³/s, max espeed: 9.7 mm/s, steps/s: 1365, steprate: 732 us, timervalue: */ 1464,
    /* Temp: 229.000000, max flowrate: 23.7 mm³/s, max espeed: 9.9 mm/s, steps/s: 1389, steprate: 719 us, timervalue: */ 1439,
    /* Temp: 230.000000, max flowrate: 24.1 mm³/s, max espeed: 10.0 mm/s, steps/s: 1412, steprate: 707 us, timervalue: */ 1415,
    /* Temp: 231.000000, max flowrate: 24.5 mm³/s, max espeed: 10.2 mm/s, steps/s: 1436, steprate: 696 us, timervalue: */ 1392,
    /* Temp: 232.000000, max flowrate: 24.9 mm³/s, max espeed: 10.4 mm/s, steps/s: 1459, steprate: 685 us, timervalue: */ 1370,
    /* Temp: 233.000000, max flowrate: 25.3 mm³/s, max espeed: 10.5 mm/s, steps/s: 1483, steprate: 674 us, timervalue: */ 1348,
    /* Temp: 234.000000, max flowrate: 25.7 mm³/s, max espeed: 10.7 mm/s, steps/s: 1506, steprate: 663 us, timervalue: */ 1327,
    /* Temp: 235.000000, max flowrate: 26.1 mm³/s, max espeed: 10.9 mm/s, steps/s: 1530, steprate: 653 us, timervalue: */ 1307,
    /* Temp: 236.000000, max flowrate: 26.5 mm³/s, max espeed: 11.0 mm/s, steps/s: 1553, steprate: 643 us, timervalue: */ 1287,
    /* Temp: 237.000000, max flowrate: 26.9 mm³/s, max espeed: 11.2 mm/s, steps/s: 1576, steprate: 634 us, timervalue: */ 1268,
    /* Temp: 238.000000, max flowrate: 27.3 mm³/s, max espeed: 11.4 mm/s, steps/s: 1600, steprate: 624 us, timervalue: */ 1249,
    /* Temp: 239.000000, max flowrate: 27.7 mm³/s, max espeed: 11.5 mm/s, steps/s: 1623, steprate: 615 us, timervalue: */ 1231,
    /* Temp: 240.000000, max flowrate: 28.1 mm³/s, max espeed: 11.7 mm/s, steps/s: 1647, steprate: 607 us, timervalue: */ 1214,
    /* Temp: 241.000000, max flowrate: 28.5 mm³/s, max espeed: 11.8 mm/s, steps/s: 1670, steprate: 598 us, timervalue: */ 1197,
    /* Temp: 242.000000, max flowrate: 28.9 mm³/s, max espeed: 12.0 mm/s, steps/s: 1694, steprate: 590 us, timervalue: */ 1180,
    /* Temp: 243.000000, max flowrate: 29.3 mm³/s, max espeed: 12.2 mm/s, steps/s: 1717, steprate: 582 us, timervalue: */ 1164,
    /* Temp: 244.000000, max flowrate: 29.7 mm³/s, max espeed: 12.3 mm/s, steps/s: 1741, steprate: 574 us, timervalue: */ 1148,
    /* Temp: 245.000000, max flowrate: 30.1 mm³/s, max espeed: 12.5 mm/s, steps/s: 1764, steprate: 566 us, timervalue: */ 1133,
    /* Temp: 246.000000, max flowrate: 30.5 mm³/s, max espeed: 12.7 mm/s, steps/s: 1787, steprate: 559 us, timervalue: */ 1118,
    /* Temp: 247.000000, max flowrate: 30.9 mm³/s, max espeed: 12.8 mm/s, steps/s: 1811, steprate: 552 us, timervalue: */ 1104,
    /* Temp: 248.000000, max flowrate: 31.3 mm³/s, max espeed: 13.0 mm/s, steps/s: 1834, steprate: 545 us, timervalue: */ 1090,
    /* Temp: 249.000000, max flowrate: 31.7 mm³/s, max espeed: 13.2 mm/s, steps/s: 1858, steprate: 538 us, timervalue: */ 1076,
    /* Temp: 250.000000, max flowrate: 32.1 mm³/s, max espeed: 13.3 mm/s, steps/s: 1881, steprate: 531 us, timervalue: */ 1062,
    /* Temp: 251.000000, max flowrate: 32.5 mm³/s, max espeed: 13.5 mm/s, steps/s: 1905, steprate: 524 us, timervalue: */ 1049,
    /* Temp: 252.000000, max flowrate: 32.9 mm³/s, max espeed: 13.7 mm/s, steps/s: 1928, steprate: 518 us, timervalue: */ 1037,
    /* Temp: 253.000000, max flowrate: 33.3 mm³/s, max espeed: 13.8 mm/s, steps/s: 1952, steprate: 512 us, timervalue: */ 1024,
    /* Temp: 254.000000, max flowrate: 33.7 mm³/s, max espeed: 14.0 mm/s, steps/s: 1975, steprate: 506 us, timervalue: */ 1012,
    /* Temp: 255.000000, max flowrate: 34.1 mm³/s, max espeed: 14.2 mm/s, steps/s: 1998, steprate: 500 us, timervalue: */ 1000,
    /* Temp: 256.000000, max flowrate: 34.5 mm³/s, max espeed: 14.3 mm/s, steps/s: 2022, steprate: 494 us, timervalue: */ 988,
    /* Temp: 257.000000, max flowrate: 34.9 mm³/s, max espeed: 14.5 mm/s, steps/s: 2045, steprate: 488 us, timervalue: */ 977,
    /* Temp: 258.000000, max flowrate: 35.3 mm³/s, max espeed: 14.7 mm/s, steps/s: 2069, steprate: 483 us, timervalue: */ 966,
    /* Temp: 259.000000, max flowrate: 35.7 mm³/s, max espeed: 14.8 mm/s, steps/s: 2092, steprate: 477 us, timervalue: */ 955,
    /* Temp: 260.000000, max flowrate: 36.1 mm³/s, max espeed: 15.0 mm/s, steps/s: 2116, steprate: 472 us, timervalue: */ 945,
    /* Temp: 261.000000, max flowrate: 36.5 mm³/s, max espeed: 15.2 mm/s, steps/s: 2139, steprate: 467 us, timervalue: */ 934,
    /* Temp: 262.000000, max flowrate: 36.9 mm³/s, max espeed: 15.3 mm/s, steps/s: 2163, steprate: 462 us, timervalue: */ 924,
    /* Temp: 263.000000, max flowrate: 37.3 mm³/s, max espeed: 15.5 mm/s, steps/s: 2186, steprate: 457 us, timervalue: */ 914,
    /* Temp: 264.000000, max flowrate: 37.7 mm³/s, max espeed: 15.7 mm/s, steps/s: 2210, steprate: 452 us, timervalue: */ 904,
    /* Temp: 265.000000, max flowrate: 38.1 mm³/s, max espeed: 15.8 mm/s, steps/s: 2233, steprate: 447 us, timervalue: */ 895,
    /* Temp: 266.000000, max flowrate: 38.5 mm³/s, max espeed: 16.0 mm/s, steps/s: 2256, steprate: 443 us, timervalue: */ 886,
    /* Temp: 267.000000, max flowrate: 38.9 mm³/s, max espeed: 16.2 mm/s, steps/s: 2280, steprate: 438 us, timervalue: */ 877,
    /* Temp: 268.000000, max flowrate: 39.3 mm³/s, max espeed: 16.3 mm/s, steps/s: 2303, steprate: 434 us, timervalue: */ 868,
    /* Temp: 269.000000, max flowrate: 39.7 mm³/s, max espeed: 16.5 mm/s, steps/s: 2327, steprate: 429 us, timervalue: */ 859,
};
#endif
// #endif

/////////////////////////////////////////////////////////////////////////////////////


void printDebugInfo();

void kill() {

    CLI(); // Stop interrupts
    disable_heater();

    printer.disableSteppers();

    // printDebugInfo();

    txBuffer.flush(true);

    for (int i=0; i<1000; i++) {
        delay(1);
        WDT_RESET();
    }

#if defined(POWER_SUPPLY_RELAY)
    POWER_SUPPLY_RELAY :: saveState();
#endif
}

void mAssert(uint16_t line, const char* file) {

    noInterrupts();
    disable_heater();
    st_disableSteppers();

    LCDMSGKILL(RespAssertion, line, file);

    txBuffer.flush();
    txBuffer.sendResponseStart(RespKilled);
    txBuffer.sendResponseUint8(RespAssertion);
    txBuffer.sendResponseUInt16(line);
    txBuffer.sendResponseString(file, strlen(file));
    txBuffer.sendResponseEnd();
    kill();
}

void killMessage(uint8_t errorCode, uint8_t errorParam /*, const char *msg */) {

    LCDMSGKILL(errorCode, errorParam, "");
    txBuffer.sendSimpleResponse(RespKilled, errorCode, errorParam);
    kill();
}

void killMessage(uint8_t errorCode, uint8_t errorParam1, uint8_t errorParam2 /* , const char *msg */) {

    LCDMSGKILL(errorCode, errorParam1, "");
    txBuffer.sendSimpleResponse(RespKilled, errorCode, errorParam1, errorParam2);
    kill();
}

// debug
void genericIntMessage(int32_t msg) {
    printer.sendGenericInt32(msg);
}

void setup() {

#if defined(REPRAP_DISCOUNT_SMART_CONTROLLER)
    lcd.setCursor(0, 0); 
    lcd.print("OK");
#endif

    CLI();

    // No watchdog for debugging, dangerous!   
#if !defined(DEBUGVERSION) 
    WDT_ENABLE();
#endif

    TIMER_INIT();

#if defined(POWER_SUPPLY_RELAY)
    // Switch on power relais to keep power
    POWER_SUPPLY_RELAY :: initActive();
#endif

#if defined(HOTEND_FAN_PIN)
    HOTEND_FAN_PIN :: initDeActive();
#endif

#if defined(MB_FAN_PIN)
    MB_FAN_PIN :: initDeActive();
#endif

#if defined(POWER_BUTTON)
    POWER_BUTTON :: init();
#endif

#if defined(LED_PIN)
    LED_PIN :: init();
#endif

    FAN_PIN :: init();

#if defined(MIN_FAN_PWM)
    // For printers where the mainboard cooling fan is connected
    // to the parts cooling fan. Keep mainboard fan running.
    printer.cmdFanSpeed(MIN_FAN_PWM, 100);
#endif

    HAL_SPI_INIT();

    rxBuffer.begin(BAUDRATE);

    tp_init();    // Initialize temperature loop

    st_init();    // Initialize stepper

#if defined(LED_PIN)
    LED_PIN :: write(255 * 0.5);
#endif

    HAL_IRQ_INIT();

    SEI();

    uint8_t retry;
    for (retry=0; retry<5; retry++) {

        if (swapDev.swapInit()) {
            break;
        }

        printer.sendGenericInt32(swapDev.errorCode()); // debug
        txBuffer.flush(true);

        WDT_RESET();
        delay(3000);
    }

    if (retry == 5) {
        LCDMSGKILL(RespSDInit, "swapInit()", "");
        txBuffer.sendSimpleResponse(RespKilled, RespSDInit);
        kill();
    }

    filamentSensor.start();

    TaskStart(taskTiming, TaskIdle);
}

//
// SDReader, read buffered stepdata from swapdevice
//

// Block-buffered sd read
class SDReader: public Protothread {

    // Buffer for block-wise reading of swap memory
    // uint8_t buffer[SD_BUFFER_SIZE];
    uint8_t *buffer;

    // Number of characters in buffer
    int16_t bufferLength;

    // Readpointer into buffer
    uint16_t bufferPtr;

    // Number of bytes to read on current thread run
    // uint16_t bytesToRead;
    uint8_t bytesToRead;

    // Temporary buffer if we cross a block boundary,
    // the size is 4 bytes - the length of the longest
    // datablock to read (see setBytesToReadX())
    uint8_t tempBuffer[4]; 

    uint16_t haveBytes;


    public:

    // Pointer to the result data, points into buffer directly or
    // to tempBuffer.
    uint8_t *readData;

    SDReader() {
        bufferLength = 0;
        bufferPtr = 0;
    }

    FWINLINE void setBytesToRead1() {
        Restart();
        bytesToRead = 1; } // Note: tempBuffer must be big enough to hold this number of bytes.
    FWINLINE void setBytesToRead2() {
        Restart();
        bytesToRead = 2; } // Note: tempBuffer must be big enough to hold this number of bytes.
    FWINLINE void setBytesToRead3() {
        Restart();
        bytesToRead = 3; } // Note: tempBuffer must be big enough to hold this number of bytes.
    FWINLINE void setBytesToRead4() {
        Restart();
        bytesToRead = 4; } // Note: tempBuffer must be big enough to hold this number of bytes.

    bool Run() {

        uint8_t i;

        PT_BEGIN();

        simassert((bytesToRead > 0) && (bytesToRead<5));
        simassert(bufferPtr <= bufferLength);

        haveBytes = bufferLength - bufferPtr;

        if (haveBytes < bytesToRead) {

            //
            // Read data from swap memory if not enough data in buffer 
            //
            if (haveBytes) {
                //
                // Copy the last bytes to temp buffer
                //
                for (i=0; i<haveBytes; i++) {
                    tempBuffer[i] = buffer[bufferPtr+i]; 
                    bytesToRead--;
                }

                //
                // Get new block from swapmem
                //
                PT_WAIT_UNTIL(swapDev.cacheFilled);

                bufferLength = swapDev.readBlock();
                buffer = swapDev.readBuffer;

                for (i=0; i<bytesToRead; i++) {
                    tempBuffer[haveBytes+i] = buffer[i]; 
                }

                readData = tempBuffer;
                bufferPtr = bytesToRead;
            }
            else {

                //
                // Buffer empty, get new block from swapmem
                //
                PT_WAIT_UNTIL(swapDev.cacheFilled);

                bufferLength = swapDev.readBlock();
                buffer = swapDev.readBuffer;

                readData = buffer;
                bufferPtr = bytesToRead;
            }

            // massert(bufferLength > 0);
        }
        else {

            // Enough data in buffer to satisfy request
            readData = buffer + bufferPtr;
            bufferPtr += bytesToRead;
        }

        PT_END();
    }

    FWINLINE uint16_t available() {

        simassert(bufferLength >= bufferPtr);
        return bufferLength - bufferPtr;
    }

    uint16_t getBufferPtr() { return bufferPtr; }

    void flush() {

        bufferLength = bufferPtr = 0;

        //
        // Restart is done in setBytesToReadX().
        //
        swapDev.reset();
    }
};

static SDReader sDReader;
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
int main(void) {

    // Call arduino init
    init();

    setup();

    for (;;) {
        loop();
    }

    return 0;
}
#endif

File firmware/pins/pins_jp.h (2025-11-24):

/*
* This file is part of ddprint - a direct drive 3D printer firmware.
* 
* Copyright 2015 erwin.rieger@ibrieger.de
* 
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
* You should have received a copy of the GNU General Public License
* along with ddprint.  If not, see <http://www.gnu.org/licenses/>.
*/

/*****************************************************************
* Jennyprinter arm shuttle gear
******************************************************************/

//
// See also:
// * maple/libmaple/timer_map.c
//

// Note: Pin nubers are the logical/mapped pins, not the physical chip pins.

#define POWER_BUTTON            DigitalInput<15, INPUT_PULLDOWN, ACTIVEHIGHPIN>  // ["GPIOA","D15","PA15"], # Power button

#define POWER_SUPPLY_RELAY      DigitalOutput<28, ACTIVEHIGHPIN>  // ["GPIOB","D28","PB12"], # Power-Relais  

#define X_STEP_PIN              DigitalOutput<18, ACTIVEHIGHPIN>  // ["GPIOB","D18","PB2"],  # X-Step
// Active state is forward direction (positive)
#define X_DIR_PIN               DigitalOutput<0, ACTIVEHIGHPIN>  // ["GPIOA","D00","PA0"],  # X-Dir
#define X_ENABLE_PIN            DigitalOutput<66, ACTIVELOWPIN>  // ["GPIOE","D66","PE2"],  # X-Enable, active low
#define X_STOP_PIN              DigitalInput<11, INPUT_PULLUP, ACTIVELOWPIN>  // ["GPIOA","D11","PA11"], # Known: Input, X-Endstop, active low
//#define X_ENABLE_ACTIVE     LOW

#define Y_STEP_PIN              DigitalOutput<46, ACTIVEHIGHPIN>  // ["GPIOC","D46","PC14"], # Y-Step
// Active state is forward direction (positive)
#define Y_DIR_PIN               DigitalOutput<70, ACTIVELOWPIN>  // ["GPIOE","D70","PE6"],  # Y-Dir
#define Y_ENABLE_PIN            DigitalOutput<47, ACTIVELOWPIN>  // ["GPIOC","D47","PC15"], # Y-Enable, active low
#define Y_STOP_PIN              DigitalInput<60, INPUT_PULLUP, ACTIVELOWPIN>  // ["GPIOD","D60","PD12"], # Known: Input, Y-Endstop, active low
// #define Y_ENABLE_ACTIVE     LOW

#define Z_STEP_PIN              DigitalOutput<69, ACTIVEHIGHPIN>  // ["GPIOE","D69","PE5"],  # Z-Step
// Active state is forward direction (positive)
#define Z_DIR_PIN               DigitalOutput<68, ACTIVEHIGHPIN>  // ["GPIOE","D68","PE4"],  # Z-Dir
#define Z_ENABLE_PIN            DigitalOutput<45, ACTIVELOWPIN>  // ["GPIOC","D45","PC13"], # Z-Enable, active low
#define Z_STOP_PIN              DigitalInput<65, INPUT_PULLUP, ACTIVELOWPIN>  // ["GPIOE","D65","PE1"],  # Known: Input, Z-Endstop, active low
// #define Z_ENABLE_ACTIVE     LOW

#define E0_STEP_PIN             DigitalOutput<1, ACTIVEHIGHPIN>  // ["GPIOA","D01","PA1"],  # E0-Step
// Active state is forward direction (positive)
#define E0_DIR_PIN              DigitalOutput<16, ACTIVELOWPIN>  // ["GPIOB","D16","PB0"],  # E0-Dir
#define E0_ENABLE_PIN           DigitalOutput<37, ACTIVELOWPIN>  // ["GPIOC","D37","PC5"],  # E0-Enable, active low
// #define E0_ENABLE_ACTIVE    LOW

// Second extruder not used 
//#define E1_STEP_PIN         36  // ["GPIOC","D36","PC4"],  # E1-Step
// Active state is forward direction (positive)
//#define E1_DIR_PIN          67  // ["GPIOE","D67","PE3"],  # E1-Dir
//#define E1_ENABLE_PIN       17  // ["GPIOB","D17","PB1"],  # E1-Enable, active low
//#define E1_ENABLE_ACTIVE    LOW

// Small fan behind hotend cooler, software switchable on newer UM2 boards.
#define HOTEND_FAN_PIN          DigitalOutput<24, ACTIVELOWPIN> // ["GPIOB","D24","PB8"],  # Known, Output, Hotend Fan (Fan 1), active low
// #define HOTEND_FAN_ACTIVE   LOW

#define LED_PIN                 PWMOutput<3, ACTIVELOWPIN>   // ["GPIOA","D03","PA3"],  # Case LED, active low

// Note: PB13 has no associated timer in stm32duino -> use bitbang temp control
#define HEATER_BED_PIN          DigitalOutput<29, ACTIVELOWPIN>  // ["GPIOB","D29","PB13"], # Heater Bed, active low

#define HEATER_0_PIN            PWMOutput<38, ACTIVELOWPIN>  // ["GPIOC","D38","PC6"],  # Heater Head 0, active low

#define HEATER_1_PIN            PWMOutput<39, ACTIVELOWPIN>  // ["GPIOC","D39","PC7"],  # Heater Head 1, active low

// #define HEATER_2_PIN        -1

#define FAN_PIN                 PWMOutput<22, ACTIVELOWPIN>  // ["GPIOB","D22","PB6"],  # Fan 0, Part cooling fan, active low

#define TEMP_BED_PIN            AnalogInput<33, 11> // ["GPIOC","D33","PC1"],  # Known: Analog Input, Temp. PT100 Sensor BED
#define TEMP_0_PIN              AnalogInput<32, 10> // ["GPIOC","D32","PC0"],  # Known: Analog Input, Temp. PT100 Sensor X
// #define TEMP_1_PIN              AnalogInput<35, 13> // ["GPIOC","D35","PC3"],  # Known: Analog Input, Temp. PT100 Sensor X 
// #define TEMP_2_PIN              AnalogInput<34, 12> // ["GPIOC","D34","PC2"],  # Known: Analog Input, Temp. PT100 Sensor, nothing connected

//
// USB OTG_HS Host, hardcoded in dd_usbh_msc.h!
//
// ["GPIOB","D30","PB14"], # DD_BOARD_USB_DM_PIN
// ["GPIOB","D31","PB15"], # DD_BOARD_USB_DP_PIN
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

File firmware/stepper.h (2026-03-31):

/*
* This file is part of ddprint - a direct drive 3D printer firmware.
* 
* Copyright 2015 erwin.rieger@ibrieger.de
* 
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
* You should have received a copy of the GNU General Public License
* along with ddprint.  If not, see <http://www.gnu.org/licenses/>.
*/

#pragma once

#include "ddprint.h"
#include "move.h"
#include "ringbuffer.h"
#include "filsensor.h"

extern int32_t current_pos_steps[NUM_AXIS];

// Initialize and start the stepper motor subsystem
void st_init();
void st_enableSteppers(uint8_t stepperMask);
void st_disableSteppers();

//
// Three different positions:
// * target pos: temp. position where we want to go to
// * planned_current_pos_steps: position where the print head is or where it should move to
// * current_pos_steps: position where the print head really is now
//   If all planned moves are done, then current_pos_steps == (last planned_current_pos_steps).
//   They are also synchronized by homing operations.
//

void digipot_init();
void digipot_current(uint8_t driver, int current);

template<typename MOVE>
void st_inc_current_pos_steps();

template<>
FWINLINE void st_inc_current_pos_steps<XAxisSelector>() {
    current_pos_steps[X_AXIS] ++;
}
template<>
FWINLINE void st_inc_current_pos_steps<YAxisSelector>() {
    current_pos_steps[Y_AXIS] ++;
}
template<>
FWINLINE void st_inc_current_pos_steps<ZAxisSelector>() {
    current_pos_steps[Z_AXIS] ++;
}
template<>
FWINLINE void st_inc_current_pos_steps<EAxisSelector>() {
    current_pos_steps[E_AXIS] ++;
}

template<typename MOVE>
void st_dec_current_pos_steps();

template<>
FWINLINE void st_dec_current_pos_steps<XAxisSelector>() {
    current_pos_steps[X_AXIS] --;
}
template<>
FWINLINE void st_dec_current_pos_steps<YAxisSelector>() {
    current_pos_steps[Y_AXIS] --;
}
template<>
FWINLINE void st_dec_current_pos_steps<ZAxisSelector>() {
    current_pos_steps[Z_AXIS] --;
}
template<>
FWINLINE void st_dec_current_pos_steps<EAxisSelector>() {
    current_pos_steps[E_AXIS] --;
}

template<typename MOVE>
uint8_t getHomeDir();

template<>
FWINLINE uint8_t getHomeDir<XAxisSelector>() {
    return printer.getHostSettings().xHomeDir;
}
template<>
FWINLINE uint8_t getHomeDir<YAxisSelector>() {
    return printer.getHostSettings().yHomeDir;
}
template<>
FWINLINE uint8_t getHomeDir<ZAxisSelector>() {
    return printer.getHostSettings().zHomeDir;
}

template<typename MOVE>
FWINLINE void st_set_direction(uint8_t dirbits) {

    if (dirbits & st_get_move_bit_mask<MOVE>())
        activate_dir_pin<MOVE>();
    else
        deactivate_dir_pin<MOVE>();
}

#define EndstopPressDebounce(spmm) max(spmm/32, 2)
#define EndstopReleaseDebounce(spmm) max(spmm/2, 2)

template<typename MOVE>
bool st_endstop_pressed();

template<>
FWINLINE bool st_endstop_pressed<XAxisSelector>() {

    static uint16_t nPresses = 0;

    if (X_STOP_PIN :: active()) {
        if (++nPresses >= EndstopPressDebounce(printer.getStepsPerMMX())) {
            nPresses = 0;
            return true;
        }
        return false;
    }

    nPresses = 0;
    return false;
}

template<>
FWINLINE bool st_endstop_pressed<YAxisSelector>() {

    static uint16_t nPresses = 0;

    if (Y_STOP_PIN :: active()) {
        if (++nPresses >= EndstopPressDebounce(printer.getStepsPerMMY())) {
            nPresses = 0;
            return true;
        }
        return false;
    }

    nPresses = 0;
    return false;
}

template<>
FWINLINE bool st_endstop_pressed<ZAxisSelector>() {

    static uint16_t nPresses = 0;

    if (Z_STOP_PIN :: active()) {
        if (++nPresses >= EndstopPressDebounce(printer.getStepsPerMMZ())) {
            nPresses = 0;
            return true;
        }
        return false;
    }

    nPresses = 0;
    return false;
}

#if defined(DualZStepper)
template<>
FWINLINE bool st_endstop_pressed<Z1AxisSelector>() {

    static uint16_t nPresses = 0;

    if (Z1_STOP_PIN :: active()) {
        if (++nPresses >= EndstopPressDebounce(printer.getStepsPerMMZ())) {
            nPresses = 0;
            return true;
        }
        return false;
    }

    nPresses = 0;
    return false;
}
#endif

template<typename MOVE>
bool st_endstop_released();

template<>
FWINLINE bool st_endstop_released<XAxisSelector>() {

    static uint16_t nRelease = 0;

    if (X_STOP_PIN :: deActive()) {
        if (++nRelease >= EndstopReleaseDebounce(printer.getStepsPerMMX())) {
            nRelease = 0;
            return true;
        }
        return false;
    }

    nRelease = 0;
    return false;
}

template<>
FWINLINE bool st_endstop_released<YAxisSelector>() {

    static uint16_t nRelease = 0;

    if (Y_STOP_PIN :: deActive()) {
        if (++nRelease >= EndstopReleaseDebounce(printer.getStepsPerMMY())) {
            nRelease = 0;
            return true;
        }
        return false;
    }

    nRelease = 0;
    return false;
}

template<>
FWINLINE bool st_endstop_released<ZAxisSelector>() {

    static uint16_t nRelease = 0;

    if (Z_STOP_PIN :: deActive()) {
        if (++nRelease >= EndstopReleaseDebounce(printer.getStepsPerMMZ())) {
            nRelease = 0;
            return true;
        }
        return false;
    }

    nRelease = 0;
    return false;
}
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

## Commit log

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2016-03-27 Use a thread to emulate serial RX interrupt, emulate rx errors, adjustments for changed rx buffer.
2016-03-27 Detect and generate error if printf() is used (in non-simulation mode).
2016-03-27 No longer using a ring buffer as the RX buffer.
    [MarlinSerial.h]
2016-03-27 Improved communication restart if SOH byte is missing.
    [MarlinSerial.h]
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2016-04-01 Filament removal: melt the plug at the end of the filament.
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2016-04-01 Reworked extrusion rate display.
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2016-04-02 Moved FillBufferTask class declaration into ddprint.h to make it available for filament sensor.
2016-04-03 Fix mintemp error on printer start.
2016-04-03 Changed datatype of filamentspeeds to int16 to get more range and precision.
2016-04-03 Changed datatype of filamentspeeds to int16 to get more range and precision. Experiment with flowrate settings - allow more slippage before feedrate limiting.
    [filsensor.cpp]
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2016-04-14 Commented unused code.
    [Configuration.h]
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2016-04-17 Adjustments for PID autotune with a 40W heater, keep fans running for faster cooldown.
2016-04-21 Added new command 'CmdEnableFRLimit' to switch on and off flowrate limiting. Mainly used to do max extrusion tests (measureTempFlowrateCurve command of ddprint.py).
2016-04-21 * Implemented new firmware command 'CmdEnableFRLimit' to switch on and off flowrate limiting. * Implemented new ddprint.py command 'measureTempFlowrateCurve' to measure a temperature vs max extrusion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
2016-05-07 * Fixed packet counter bug: garbled data was sometimes interpreted as CmdResetLineNr. * Some cleanup
    [ddprint.cpp]
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2016-05-07 * Removed old AutoTemp algorithm. * Added material profile overrides. * Moved 'extrusionAutoTempFactor' from nozzle profile to material profile.
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2016-05-16 measureTempFlowrateCurve(): Use gnuplot 'fit' function to determine the 'extrusionAutoTempFactor' for material profiles.
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2016-05-27 Added assertion if flowrate gets to low (small nozzles) - need to fix this.
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2016-09-02 Rework class Move, splitted it into TravelMove and PrintMove.
2016-09-02 Fixed Makefiles, added ard-parse-boards script and PARSE_BOARD variable.
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2016-09-22 Fixed extrusion values.
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2016-10-13 Move.leadAxis(): Use top speed to determine leadAxis if x- and y-axis have the same step amount.
2016-10-13 Rework computation of stepper direction bits.
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2016-10-16 Fix timer overflow in decelRamp().
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2016-10-22 Fix timer overflow in planCrossedDecelSteps().
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2016-10-28 Fix debug trace.
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2016-10-28 Stepper ISR: set new timer value as fast as possible, to prevent timer overflow and irregular steps.
    [stepper.h]
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2016-11-24 Added new firmware command CmdGetDirBits to request current stepper direction pin state from printer.
2016-11-24 Re-enabled ADNS9800 filament sensor. Added new firmware command CmdGetDirBits to request current stepper direction pin state from printer.
2016-11-24 Re-enabled ADNS9800 filament sensor. Use a exponential filter to average measured filament feedrate.
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2016-11-26 Added new firmware command CmdGetDirBits to request current stepper direction pin state from printer. Some cleanup.
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2016-11-26 Added methods to query stepper direction pins (for CmdGetDirBits), renamed INVERT_x_DIR config to POSITIVE_x_DIR.
    [Configuration.h]
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2016-12-14 Compress datastream between host and firmware: Send accelramps, decelramps and raw stepper data in form of 1 byte deltas instead of 2 byte words, if possible.
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2016-12-15 Replaced zmodem crc16 by kermit ccitt crc16. This algorithm is about 25% faster.
    [ddprint.cpp]
2016-12-15 Increased baudrate to 500000. Baudrate 115200 is not enough for fast prints together with advance. Baudrate 230400 is not a 'natural' baudrate for the Mega2560. Baudrate 250000 does not work with pys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
    [Configuration.h]
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2016-12-23 Cleanup: Removed unused code. Bugfixing filament slip compensation.
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2016-12-30 Added new material profile setting "kFeederCompensation" for filament slip compensation.
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2017-01-02 * Override slicer settings per commandline. * Added debug flag * Ignore cura's current user settings - temporary changes in the gui should not influence the slicing per commandline.
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2017-02-09 Small fix: limit timervalue to 16 bit.
2017-02-09 * removeFilament(): feed more material to remove retraction blob. * Added downloadDummyTempTable() to avoid speed limiting while measuring flowrate curves. * Some fixes for measureTempFlowrateCurve().
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2017-02-21 Cleanup: removed unused code.
    [Configuration_adv.h]
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2017-02-23 Removed ewma filter for feeder target speed. Call filamentsensor run() method every 10ms instead of every 100ms to improve the response time of the speed measurements.
2017-02-23 Removed ewma filter for feeder target speed. Use simple running average filter for measured filament speed.
2017-02-23 Rework filament sensor calibration. Use a table of calibration values for different feedrates instead of a single value.
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2017-02-24 Added methods to compute flowrate sensor values. Rework temp-flowrate interpolation code.
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2017-02-25 Reworked Auto-Temp code, use max flowrate of time interval instead of average.
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2017-03-04 Config: Added *debugAdvance* flag to enable/disable debug traces of the advance module.
2017-03-06 Decreased BED_MAXTEMP from 200 to 150.
    [Configuration.h]
2017-03-09 Added script to generate the termistortable for the ultimaker2 board (pt100 with INA826 amplifier).
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2017-03-10 Reworked hotend temperature PID controller: * Cleanup integral windup code. * Tuned PID parameters for no over-/undershoots. * Added pwmSum for better handling of pwm clipping. * PID debugging * Bett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
    [Configuration.h]
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2017-05-12 Changes for reworked errorhandling in SDCard library.
    [ddcommands.h, ddprint.cpp]
2017-05-12 Rework errorhandling in case of SD (read) errors.
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2017-06-27 Determine filament slipping amount by ratio of feeder steps and measured filament movement.
    [ddprint.cpp, filsensor.cpp]
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2017-06-28 Filamentsensor: removed reset of positions on retract.
    [ddprint.cpp, filsensor.cpp]
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2017-06-28 Use new filament slippage calculation in measureTempFlowrateCurve().
2017-07-20 Replaced "targetExtrusionSpeed" and "actualExtrusionSpeed" with "slippage" value in printer status message.
2017-07-25 Updated comments, fixed usage message, use "quality" containers to resolve material profile also.
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2017-12-10 Improved error reporting in case of a SD card read error. Return SPI statusbyte too.
    [ddprint.cpp, filsensor.cpp]
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2017-12-31 Adjustments to new arduino version 2:1.0.5+dfsg2-4 and code cleanup.
    [Configuration.h]
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2018-01-02 Fixing arduino SPI library problem: interrupts are globally masked during SPI transactions.
    [filsensor.cpp]
2018-01-03 Fixing arduino SPI library problem: implement own SPI driver class 'DDPrintSpi' for SdFat and FilamentSensor.
2018-01-03 Replace Arduino SPI library with own implementation.
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2018-01-03 FilamentSensor: Replace Arduino SPI library with own implementation.
    [filsensor.cpp]
2018-01-03 SwapDevice/SdFat: Replace Arduino SPI library with own implementation.
2018-01-04 Handle SD card error messages from printer.
2018-01-04 Handle SD card read errors (CRC), retry block read.
    [ddprint.cpp]
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2018-01-13 Rework validation of SROM_ID.
    [filsensor.cpp]
2018-01-18 Filament flowrate measurement: don't reset when filament is going backwards (retract, lin-advance). Else it will disturb the measurements too much.
    [filsensor.cpp]
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2018-01-18 Rework calibrateFilSensor() and some cleanup.
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2018-02-21 Rework measurement of hotend temperature step response.
2018-02-21 Rework pid controller, added COBias for bumpless setpoint changes.
    [ddtemp.cpp]
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2018-02-21 Rework flowrate measurement, limit feedrate using a square function.
    [filsensor.cpp]
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2019-03-01 TUI: minor fix of bed temp display.
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2019-05-18 Rework testFilSensor() to use args.feedrate and to use filament sensor calibration factor from printer profile *FilSensorCalibration*. Re-activated calibrateFilSensor().
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2019-05-21 Cleanup printvolume dimensions, removed unused stuff.
    [Configuration.h, Configuration_adv.h]
2019-05-21 Fixed cast/integer overflow.
    [Configuration.h]
2019-05-22 Added new commands CmdSetFilSensorCal and CmdSetStepsPerMME. Rework computation of filament slip.
    [ddprint.cpp, filsensor.cpp]
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2019-05-25 * Removed support for ADNS9800 optical mouse sensor and Bourns ems22a Rotary Encoder as flowrate sensors. * Renamed MarlinSerial to SerialPort * Start Hotend Fan of newer ultimaker 2 boards (connecte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
    [config.h, ddprint.cpp, filsensor.cpp]
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2019-06-02 Rework comments, removed unused code.
    [ddprint.cpp, pins_um2.h]
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2019-06-10 Re-measured zaper petg silver with new/fixed filament sensor.
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2019-06-10 Rework testFilSensor() and calibrateFilSensor().
2019-06-11 Rework filament sensor code, cleaner and simpler.
    [ddcommands.h, filsensor.cpp]
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2019-07-27 Some cleanup.
    [Configuration.h, Configuration_adv.h]
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2019-12-27 Avoid pressure advance for infill moves.
2019-12-27 Cleanup gcode type handling. Parse segment type comments in gcode to avoid pressure advance for infill moves.
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2020-01-14 Ddprintui: added control for *extrusion rate*, several minor UI-fixes.
2020-01-15 Added comment.
    [Configuration.h]
2020-01-15 Increased endstop clearance from 0.1mm to 0.25mm.
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2020-01-16 Serial interface: disable HUPCL to avoid reset of printer on serial open.
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2020-01-16 Rework/cleanup measureTempFlowrateCurve funktion. Debug traces: be less verbose.
2020-01-20 Added new ddprint command *testFeederUniformity* to check the smoothness of the filament sensor readings (wobbly sensor wheel).
2020-01-28 save work
    [Configuration_adv.h]
2020-03-13 Save work.
    [Configuration.h]
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2020-03-24 Rework printerinit and printer state handling.
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2020-03-24 Rework printerinit, some cleanup.
2020-03-25 Cleanup: removed unused code and configuration_adv.h.
    [Configuration.h, Configuration_adv.h]
2020-03-25 Cleanup stepdir/enable pin handling.
    [Configuration.h, Configuration_ramps.h, Configuration_um2.h]
2020-03-26 Rework/cleanup stepdir/enable pin handling.
    [Configuration.h]
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2020-03-31 Removed unused adns9800 sources. Added license headers. Some cleanup.
    [Configuration.h, Configuration_ramps.h, Configuration_um2.h]
2020-04-01 Added feedsensor.stl 3d model.
    [feedsensor.stl]
2020-04-01 Minor change: rotated model.
    [feedsensor.stl]
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2020-04-01 Fixed handling of printer name in pre(processing) mode.
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2020-04-08 Fixed uint16 range overflow in CmdSyncHotendPulse.
    [ddprint.cpp]
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2020-04-12 Added some documentation and added dual feeder 3d model.
    [dual_holder.scad, dual_holder.stl]
2020-04-26 Rework CLI for feeder calibration/test commands.
2020-04-26 Rework/fix CLI for *heatHotend* command.
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2020-07-03 Minor changes on error message and debug traces.
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2020-07-03 RemoveFilament function: increase hotend temp to better melt filament plug.
2020-07-03 Hotend temperature: improve "pwm hinting" to prevent hotend overtemp.
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2020-07-03 Rework printing process, move preloading and statemachine.
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2020-07-03 Cleanup and rework autotemp, use p0temp from material profile as base temperature.
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2020-07-03 Fixed bug with wrong stepper direction bits (introduced with new dwellms command). Cleanup hotend fan control. Updated some comments. Update simulator: use std namespace for amd64 compile.
    [ddprint.cpp]
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2020-07-03 New commandline arg *-t* to skip heatup delay.
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2020-07-03 Fix download of dummy temptable to disable temperature limiter for measurements.
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2020-07-10 Porting JennyPrinter: sending on usb-serial.
    [Configuration.h]
2020-07-19 Porting JennyPrinter: fix jump-to-bootloader.
    [ddprint.cpp, hal_arm.h]
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2020-07-25 Porting JennyPrinter: Various changes * More work on pin-mapping * PWM outputs: LED, FAN, Heaters * More work on STM32 Hal * Re-enabling code
    [Configuration.h]
2020-07-26 Porting JennyPrinter: Rework/cleanup pins handling.
    [ddprint.cpp, ddtemp.cpp, fastio.h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]
2020-07-26 Various changes: * More work on pin-mapping * More work on HAL's * Re-enabling code
    [Configuration.h]
2020-07-27 Work on temp. measurement and pins for AVR boards.
    [Configuration.h]
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2020-08-09 Restructuring directories, fix avr build.
    [hal_arm.h, hal_avr.cpp, hal_avr.h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]
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2020-08-16 Removed unused stuff.
    [Configuration.h]
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2020-08-17 Fix calibrateESteps().
2020-08-18 CalibrateFilSensor command: removed printer commandline parameter. Some fixes for measureHotendStepResponse().
2020-08-18 JennyPrinter: added missing temperature table entries.
    [thermistortables.h]
2020-08-18 JennyPrinter: Fixed temperature measurement pins and direction of E axis.
    [pins_jp.h]
2020-08-18 Fixed *pwmMode*, needed for *PID autoTune* command.
    [ddtemp.cpp]
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2020-08-21 Added a *heatUpRamp()* method to avoid the big temperature overshoot when heating up hotend.
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2020-08-22 Cleanup, removed unused stuff.
    [Configuration.h]
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2020-08-22 Added emergency reset command.
    [ddcommands.h, ddprint.cpp, hal_arm.h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]
2020-08-22 Rework pid autotune and added computation of PID parameters with the *T-sum* method.
2020-08-23 Pid settings: Use two PID value sets for different tasks. A fast one for printing and a slow one without big overshoot for measurement purposes.
2020-08-24 Slower heater pwm to work around hardware problem (slow mosfet driver).
    [hal_arm.h]
2020-08-24 Reworking temperature stuff and filament measurement. Some fixes and cleanup.
2020-08-24 New method for intoair filament measurement, using a fixed PWM value.
2020-08-25 Re-enabling/fixing printing and e-step calibration.
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2020-09-14 Fix gradual advance mode (for k-advance calibration).
2020-09-20 Arduino compress problem.
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2020-10-08 Some smaller timer fixes.
    [hal_arm.h]
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2020-10-09 Mainloop: revert debug changes.
    [ddprint.cpp]
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2020-10-21 Rework UnZipper <-> SwapDev interface.
    [config.h, ddprint.cpp]
2020-10-24 Fix avr mega build.
    [config.h, ddprint.cpp, stepper.h]
2020-10-26 Disable heater,stepper,interrupts before mAssert(). Avoid running heaters if a breakpoint is set on mAssert().
    [ddprint.cpp, stepper.cpp, stepper.h]
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2020-11-01 Zwei probleme: * underrun bei schnellem start (ohne nützliche aufwärmphase) * fehler bei abort usb write10 (memory corruption?)
    [config.h, ddprint.cpp, hal_arm.h]
2020-11-08 Using block reset to cancel write request, use clear feature to reset input and output endpoints.
    [ddprint.cpp, usbh_def.h]
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2020-12-03 Minor fixes of debug traces.
2020-12-04 Minor fixe: changed pretty print of printer status.
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2020-12-09 Rework handling of wasEmpty flag to avoid assertion on print-start.
    [stepper.h]
2020-12-11 Tempcontrol: rework handling of pwm hint (suggestedPwm).
    [ddtemp.cpp]
2020-12-12 Gradual advance factor: reworked to use sequential print instead of layerchange to increase advance factor.
2020-12-14 Cleanup, rework eot handling.
    [ddprint.cpp]
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2020-12-26 Disabled fixed pid mode.
2020-12-31 Rework temperature measurement and tempcontrol: * Class RunningAvgF: lower temperature averaging window to 0.25s * pid: fix differential term: distribute dTerm 'energy' instead of cutting it. * suppo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
    [ddprint.cpp, ddtemp.cpp]
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2021-01-04 Rework calibrateFilSensor().
2021-01-04 Rework filament measurements.
2021-01-08 Fix bug with break in measure filament.
2021-01-08 Rework handling of filament sensor readings.
    [config.h, ddprint.cpp, ddtemp.cpp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]
2021-01-08 Fix +-1 problem with filsensor readings index.
    [ddprint.cpp, filsensor.cpp]
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2021-01-15 Rework autoTemp: basetemp now depends on workingPonint (wp=0: figurine print, wp=1: parts print).
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2021-01-29 Cleanup generic material profiles, don't intend to use 3mm filament so it is no longer neccessary to keep two versions of them.
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2021-01-31 Fix autotemp: less debug traces, faster.
2021-01-31 Rework auto-temp if flowrates are better when printing than into-air.
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2021-02-04 Fix bug with disabled autotemp, some cleanup.
    [ddprint.cpp]
2021-02-06 Ramps: re-enable stuff, cleaup and fixes. Remove wait states for avr.
    [config.h]
2021-02-06 Ramps: re-enable stuff, cleaup and fixes.
    [ddprint.cpp]
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2021-02-06 Mass-storage read on sdcard: added wrapper-layer and cleanup error/return code handling.
    [hal_arm.h]
2021-02-06 Rework commandline arguments as lower case.
2021-02-07 ddprint tui: Minor fixes: add print duration to printlog, display undergrip and undertemp values in.
2021-02-08 Ramps: minor improvements, cleaup and fixes.
    [filsensor.cpp, stepper.h]
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2021-02-14 Rework slippage calculation, filter noise/glitches. Some cleanup.
    [filsensor.cpp]
2021-03-05 Minor format fix of printlog.
2021-03-06 Adding new board: rambo.
    [Configuration.h, Configuration_ramps.h, Configuration_um2.h]
2021-04-05 Rework/cleanup TXBuffer: * send only one message per thread-run -> simpler code with same functionality * changed ringbuffer interface * removed old stuff, added comments
2021-06-09 Merge fix-avr into master.
    commit e19423812638afecaef0a137a49ecc404a50dd18
    Author: ErwinRieger <erwin.rieger@ibrieger.de>
    Date: Wed Jun 9 17:15:20 2021 +0200
    Removed debug-trace.
    commit 31619c3a281982fcb4a4c3836a807bbbbb427e47
    Author: ErwinRieger <erwin.rieger@ibrieger.de>
    Date: Wed Jun 9 14:38:55 2021 +0200
    Fixes for jennyprinter/stm32 after avr-fix merge.
    commit cdccd3617ce3a4ed3f1e93e9f28cb090a6f4ff3e
    Author: ErwinRieger <erwin.rieger@ibrieger.de>
    Date: Wed Jun 9 13:20:57 2021 +0200
    Rework arduino-cli dependency.
    commit 54c2f1160d67098d7a62f41c5dbcbf7153ef7448
    Author: ErwinRieger <erwin.rieger@ibrieger.de>
    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
    [Configuration.h]
2021-06-11 Fixed argparse error on raspberry.
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2021-06-25 Minimal distance for FRS measurement (fsrMinSteps): Replace fixed value with a computed one.
    [filsensor.cpp]
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2021-09-02 Removed old models.
    [dual_holder.scad, dual_holder.stl]
2021-09-02 Reworked flowrate sensor housing: * Rotated design to shorten filament path between feeder gear wheel and rotary encoder for better response. * Made it i bit more compact.
    [feedsensor-anycubic.stl, feedsensor-bmg.stl, feedsensor-um2.stl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]
2021-09-02 Rotate model for easier slicing.
    [feedsensor-anycubic.stl, feedsensor-bmg.stl, feedsensor-um2.stl]
2021-09-16 Porting ddprint to Ender5 (pro):
    * Changes for the Creality melzi board (atmega1284p based).
    * Added thermistor table for epcos 100k ntc.
    * Declared IO-pins in firmware/pins_ender3.h
    * Rework homing:
    + use feedrate and direction for homing from printerprofile.
    + Move away from nozzle after z is homed (for printers that
    home at z=0. This is to avoid scratching over the bed when
    homing X and Y.
    + Homing: added "4 point mode" for ender.
    * Added new script *thermistor_table.py* to generate thermistor
    tables (c-code).
    Other changes:
    * Host: rework *getstatus* and *mon* commands.
    * Host: filament profile measurement:
    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
    [Configuration.h]
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2021-10-15 Merged next branch into master.
    Simplified and fixed handling of first layer bed temperature.
    Rework and fix homing: z-height was set to high, this lead to a z-endstop error.
    Added new config var "HOMEZLIFT".
    Experimental feature: keep bed warm after print (eg don't cooldown).
    This is to avoid glas-chipping when printing petg on a glass bed. Two
    new profile entries for this: *bedSurface* and *keepBedtemp*.
    Rework sdcard erase, fix compilation for stm32.
    Added "heatbed" ddprint command.
    ddprintui.py: fix missing printing state.
    Removed ultimaker "ulti gcode" stuff.
    Re-enable watchdog.
    [ddprint.cpp]
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2021-10-27 Planner: fix bug when no material profile is used.
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2021-11-15 * Rework ddprofile.py: move from singleton classes to normal class instances. * Overall cleanup: removed debug traces. * Gcodeparser: accept (and ignore) M201, M203 and M205 gcodes. * Gcodeparser: Ha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
2021-12-07 Documentation: * Update section about auto-temp. * Fix section links * Added more pictures * Added information in flowratesensor section * Added flowratesensor details section * Added information in 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
2021-12-30 Fixed mAssert() and killMessage() for ramps and rumba boards.
    [ddprint.cpp]
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2021-12-30 Clean up Printer class interface, python3 fixes for some debug-code.
2022-01-14 Merge anycubic-i3m branch:
    Anycubic i3m port:
    * Pin changes for anycubic i3m.
    * Add support for ATC Semitec 104GT thermocouple.
    * Homing: add support for additional Z1 stepper motor and endstop.
    * Homing: implement dual-z homing.
    * Adjust getendstops command for the additional Z-endstop.
    * Control mainboard cooling fan (anycubic i3m).
    * Rework temperature measurement: allow
    different thermocouple types for heated bed
    and hotend.
    * Changed initial baudrate to 500 kbaud, 1 Mbaud is to fast for
    Anycubic i3m.
    * Auto-baudrate: added new printer profile setting
    'baudRateLimit' for the Anycubic i3m (it does not work
    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
    [Configuration.h]
2022-01-14 printer.getFSReadings(): fix integer division (python3).
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2022-01-15 Filament measure2: * Disable flowrate limiter after initial layers are printed. * Fixed some integer divisions (python3). * Stop measurement if a speedup of 2x is reached. * Improved error-handline a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
2022-01-16 Gcodeparser: removed debug trace message, better errorhandling.
2022-01-18 Renamed flowrate sensor STL's.
    [feedsensor-in_E3D-out_M6.stl, feedsensor-in_M6-out_M6.stl, feedsensor-in_UM2-out_M6.stl]
2022-01-18 Renamed flowrate sensor STL models, using new naming scheme.
    [feedsensor-in_E3D-out_M10.stl, feedsensor-in_M6-out_M10.stl, feedsensor-in_UM2-out_M10.stl]
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2022-01-30 * Simplify FRS measurement, removed MinExtrusionForMeasurement, mark every extruding move as a measuring move. * New firmware build. * Replace own isclose() with math.isclose() and other code cleanup.
    [ddcommands.h, ddprint.cpp, filsensor.cpp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]
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2022-02-07 * Rework/simplify FRS measurement, removed MeasureStartBit flag, removed 0.1s measurement interval. * Rework filament measurement: + Moved measureTempFlowrateCurve() and measureTempFlowrateCurve2() t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
    [ddcommands.h, ddprint.cpp, filsensor.cpp]
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2022-02-09 Use syncronized command to switch of heaters at end of print, this fixes issue "Endofprint: turn of heaters with a synchronized command #6".
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2022-02-10 Firmware: cmdSetIncTemp(): fix assertion.
    [ddprint.cpp]
2022-03-10 Filament measurement 2: Reverted to previous method to determine the fixed hotend PWM value used for measurement.
2022-03-14 Keep bed temp at end of print: fix typo.
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2022-04-02 Fix: Planner: don't use materialProfile if no material profile is specified.
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2025-11-24 feat: Squash merge from next branch
    This commit squashes all the changes from the branch into a single commit.
    The changes include:
    - Rework filament measurement
    - No homing for manual extruder moves
    - Debug extruder grip
    - Enabled usb-debugging
    - Debugging usb storage
    - Cleanup
    - Changed Dir-pin for extruder motor
    - Fix alpha value in plt.fill_between() call
    - Keep bed running after print (for petg)
    - Increase hotend max temp to 290 °C
    - Handle parity errors when reading filament sensor position
    - Wait until temperature average is valid for second filament measurement
    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
    [Configuration.h]
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2025-11-25 feat: Squash merge from feature-getversion branch
    - Reimplement getVersion command to no longer use git-hash, but a word-count of the source-code.
    - Added a new script .
    - Compare local source version with firmware version and emit a warning if they do not match.
    - Fixes for older python3 versions.
    - Rebuild firmware images.
    - Ignoring temp. build files.
    - Fix: adjust filsensor mockup to new class interface.
    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
    [ddprint.cpp]
2026-02-07 * Fix endstop handling for dual-stepper machines (anycubic). * Added new error code "RespEndstopError".
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

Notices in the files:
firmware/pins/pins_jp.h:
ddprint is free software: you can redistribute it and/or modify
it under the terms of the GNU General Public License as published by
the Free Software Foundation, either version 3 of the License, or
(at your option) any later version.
